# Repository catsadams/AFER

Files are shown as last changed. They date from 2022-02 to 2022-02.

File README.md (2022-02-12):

# AFER
Design and development of  Autonomous Feline Entertainment Robot(AFER) - Project Files
Advanced Control Systems - University of West Florida - Spring 2021

Conference paper abstract
Abstract—The aim of this paper is to present the design and development of a safe and reliable autonomous cat toy for the purposes of entertaining pet cats when human interaction is not feasible. The proposed Autonomous Feline Entertainment Robot (AFER), an autonomous cat toy, is comprised of a table-mounted base, and a robotic arm with two linkages. The AFER Version 1(v1) has a cat-toy affixed to the end of a linkage as the end effector, while the AFER Version 2 (v2) has a passive joint with a string to which a cat toy end effector is attached.  The AFER v1 has 2 Degrees of Freedom (DOF), while the AFER v2 has 3DOF, and both are actuated by servomotors interfaced with an Arduino microcontroller. In order to enable maximum functionality, the AFER is designed with multiple movement patterns or modes for play, as well as the ability to change the specific end effector of the toy. Position control was used for the motion and trajectory planning when developing the movement patterns. The interaction between AFER and two kittens has been evaluated in an experimental scenario, and the results show satisfactory and safe interactions. The AFER can be used as a model for studying effective animal-robot interactions and pet entertainment.

Conference Paper Directory Includes: PDF of final paper, LaTex text files and images pulled for conference paper
Matlab-Arduino Directory Includes: Matlab, Simulink, Arduino code 
CAD Renderings Directory Incudes: SIMULINK renderings of the robot

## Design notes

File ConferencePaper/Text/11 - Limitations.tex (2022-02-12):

There were considerable limitations to this work including lack of access to a robotics lab due to COVID-19 restrictions; as a result, this robot was developed, built, and tested, entirely with at-home robotics equipment. This severely limited the choice of materials and opportunity to attempt multiple builds. 
Additionally, several necessary base assumptions made limited the scope and real-world applicability portions of the work, particularly for the v2. The assumptions for J3 were significant, yet necessary given the circumstances. As a result, the mathematical model for AFER v2 was not able to account for random motion or vibrations of the string, and, therefore, it was not possible to account for those disturbances while planning movement patterns. Additionally, the lack of an encoder on the passive joint, J3, meant that interpreting the success of the movement patterns in any way other than visual, was not possible.
Finally, the preference analysis conducted was based on only two cats and the testing was not repeated multiple times to ensure consistency. A much larger sample size with repetitive testing events would be needed for robust, statistically significant analysis on animal preferences between movement patterns and end effectors \cite{laschi2006design}.

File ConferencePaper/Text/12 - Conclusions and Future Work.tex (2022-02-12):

\subsection {Conclusions}
We developed a simple entertainment robot (two versions) to entertain animals (cats) when they are not attended by humans. Despite limited access to materials, the concepts of the robots were shown to be viable, and the kittens/cats were safely engaged and enjoyed playing with the toy actuated by the robot for as long as the robot was operational. The study is new in the robotics field and possesses significant potential to be used enormously to enhance the entertainment, companionship, and well-being of companionship animals.

\subsection {Future Work}
As expected, prototype models of systems had many issues and often required multiple redesigns and repairs; the AFER systems were no different. Unfortunately, redesigns and more robust construction were beyond the scope of the research in its current iteration. The following issues were identified with the design and would need to be addressed in any future work.
     \par The connection at J1 was small and unstable, and a structural redesign of the robot with a more robust joint or additional support material is necessary for any further work. A redesigned system in conjunction with improved modeling procedures would enable refinement of the control algorithm, and lead to better performance. Additionally, implementing more complex movement patterns would increase applicability.
Due to the nature of the end effector attachment on v1, the computer and electrical components of the system needed to be placed on the ground. For a system that is expected to entertain pets, this is not acceptable. In future iterations, implementing control with a localized chip and batteries would be ideal. If this is achieved, the AFER base could be mounted on a mobile robot unit for further autonomous functionality.
    \par The interactions between cats and the robots will need to be videotaped, which will allow further analysis of the behaviors of the cats with the robots. Machine learning methods such as the reinforcement learning, inverse reinforcement learning or deep reinforcement learning will be used to learn the behaviors of the cats with the robots, which may suggest significant improvements in the design and controls of the robots.

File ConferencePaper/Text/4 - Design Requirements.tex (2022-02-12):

Given the intended use of the AFER platform, the design could not be overly complex and could not require components that would be difficult to acquire for the average person. The robot required the ability to move a cat toy end effector in several, distinct movement patterns for maximum engagement with the animals. 
The robot design also needed adequate safety precautions integrated into the design to prevent injury during operations. The joints and linkages needed adequate softness to prevent injury in the event that the robot made contact with an animal during the course of operations, and any components relating to the control such as wires would be designed such that the animals will not be able to access them.

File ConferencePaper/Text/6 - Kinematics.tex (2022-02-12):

For both versions of the robot, the transformation matrix values were determined using Denavit–Hartenberg (DH) parameters. When solving the kinematics for both v1 and v2, the length of the common normal was identified by the variable r to avoid confusion between variables a and $\alpha$. 

\subsection{Robot Configuration Overviews}
AFER v1 was a 2-DOF robot, actuated by servomotors and an Arduino controller, and modeled such that the cat toy end effector formed a rigid linkage with \textit{l2}. The robot utilized a revolute base joint (J1) and a revolute lift joint (J2) to move the end effector as commanded; the chosen joint configuration allowed the robot to operate along the edges of a hemispherical work envelope with a surface area of $39.9ft^2$, situated about the robot’s center, shown in Fig.5.

\begin{figure}[h!]
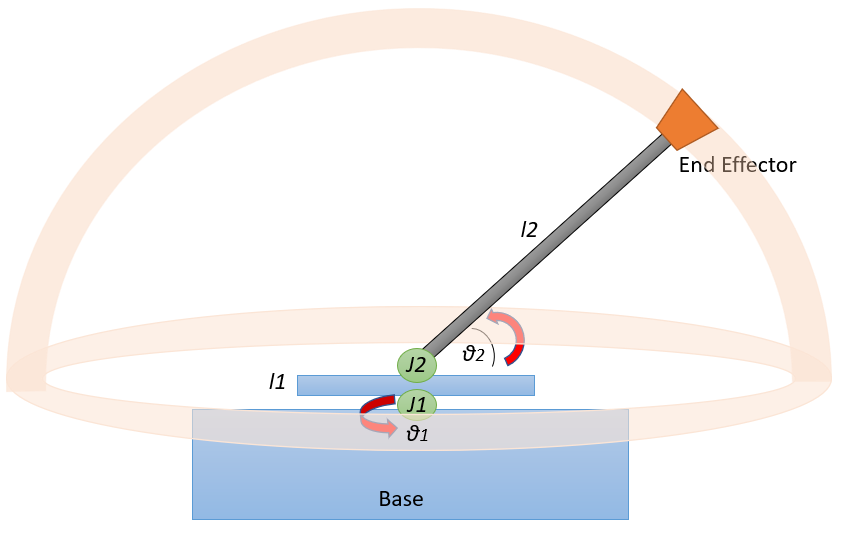
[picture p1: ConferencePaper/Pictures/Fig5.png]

\caption{AFER v1 Work Envelope.}
\label{fig5}
\end{figure}

For this version of the robot, the end effector was mounted directly to \textit{l2}. As the arrangement caused no considerable difficulty when solving the kinematic equations, the mathematical modeling used for v1 closely resembled the real-world robotic build, and the assumptions when solving the kinematic equations were minimal. 
For AFER v2 as shown in Fig.6, the cat toy end effector attached to the rest of the robot via J3, a frictionless joint that was passive in the pitch direction and had no damping. The chosen joint configuration allowed the robot to operate along the edges of a hemispherical workspace with a surface area of $39.9 ft^2$, situated about the robot’s center. The workspace size of v1 and v2 were identical, however the v2 workspace was lower due to the introduction of \textit{l3}. 

\begin{figure}[h!]
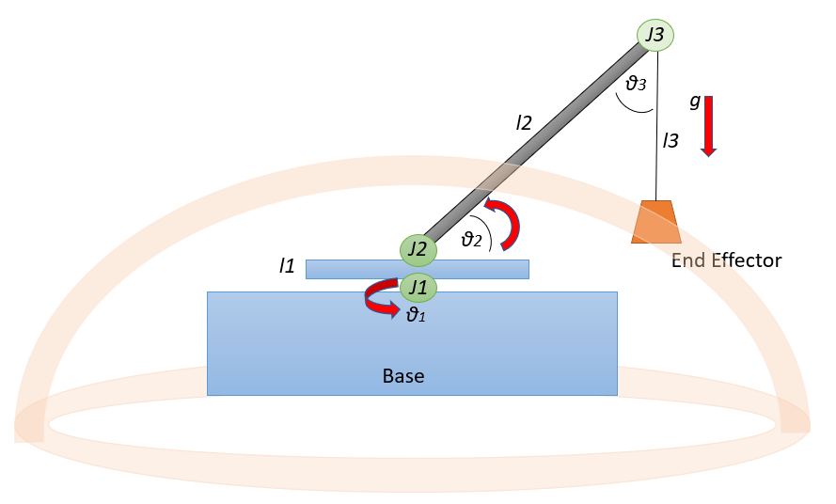
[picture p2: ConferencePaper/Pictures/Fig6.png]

\caption{AFER v2 Work Envelope.}
\label{fig6}
\end{figure}

Realistically, the string attached to the J3 joint on AFER v2 was able to move freely and had factors such as elasticity and conflicting multi-modal vibrations. However, it caused the kinematic equations to be non-linear and extremely difficult, if not impossible, to solve. Therefore, in order to ensure that the kinematics for this version of the robot were useful and solvable, J3 was modeled as a passive joint on a rigid link instead of a compliant linkage. Additionally, the momentum was discounted and the gravity(g) was assumed to be the only force acting upon the suspended end effector. 

\subsection{AFER v1 Forward Kinematics}
The forward kinematics for v1 as a 2-joint robot were relatively simple, but to ensure the solvability of the kinematic model, static stability was assumed for all points. Using the coordinate frames as shown in Fig.5, creating a transformation matrix from the base of the robot to the end effector using a link coordinate diagram was straightforward. The transformation values of r, $\alpha$, d, and $\theta$ are given in Table ~\ref{table:1}.

\begin{center}
\begin{table}[h!]
\centering
\caption{DH PARAMETERS FOR AFER v1}
   \begin{tabular}{ | c | c | c | c | c | }
   \hline
    Point & $d_{i}$ & $\theta_{DHi}$ & $r_{i}$ & $\alpha_{i}$ \\ \hline
    J1 & 0 & 0 & 0 & 0  \\ \hline
    J2 & \textit{l1} & $\theta_{1}$ & 0 & 0 \\ \hline
    EE & \textit{l2} & 0 & 0 & $\theta_{2}$\\ \hline
    \end{tabular}
		\label{table:1}
\end{table}
\end{center}

AFER v1 had a horizontal stroke equal to the length of \textit{l2} and a vertical stroke of \textit{l1} + \textit{l2}. Additionally, the absence of linear actuators indicated that the di values were static. The transformation from the coordinate frame at J1 to the coordinate frame at the end effector was determined as shown in \eqref{1}:

\[
\centering
\begin{bmatrix}
cos\theta_{1} & -sin\theta_{1}cos\theta_{2} & sin\theta_{1}sin\theta_{2} & 0\\
sin\theta_{1} & cos\theta_{1}cos\theta_{2} & -cos\theta_{1}sin\theta_{2} & 0 \\
0 & sin\theta_{2} & cos\theta_{2} & \textit{l2} + \textit{l1} \\
0 & 0 & 0 & 1 \\
\end{bmatrix}
\begin{equation}
\label{eq1}
\end{equation}
\]

\subsection{AFER v2 Forward Kinematics}
The forward kinematics for AFER v2, a 3-joint robot, were relatively simple. When solving the kinematics, static stability was assumed. The DH parameters for J1, J2, and J3 in v2 were identical to the DH parameters for J1, J2 and the end effector (E) of v1 due to the common core configuration of the robot. The values for v2 DH parameters are listed below in Table ~\ref{table:2}. 

\begin{center}
\begin{table}[h]
\centering
\caption{DH PARAMETERS FOR AFER v2}
    \begin{tabular}{ | c | c | c | c |c | }
    \hline
    Point & \ $d_{i}$ & $\theta_{DHi}$ & $r_{i}$ & $\alpha_{i}$ \\ \hline
    J1 & 0 & 0 & 0 & 0  \\ \hline
    J2 & \textit{l1} & $\theta_{1}$ & 0 & 0 \\ \hline
    J3 & \textit{l2} & 0 & 0 & $\theta_{2}$\\ \hline
		E & -\textit{l3} & 0 & 0 & $\theta_{2}+ \frac{\pi}{2}$ \\ \hline
    \end{tabular}
		\label{table:2}
\end{table}
\end{center}

As in v1, v2 had a horizontal stroke equal to the length of \textit{l2}; however, the vertical stroke of \textit{v2} was equal $\textit{l1} + \textit{l2} – \textit{l3}$. Given that there were no linear actuators, the $\textit{d}_{i}$ values were static. The transformation from the coordinate frame at J1 to the coordinate frame at the end effector(E) for v2 was determined as shown in \eqref{2}, where $(\alpha_{E} = \theta_{2} + \frac{\pi}{2})$.

\[
{\tiny
\centering
\label{eq2}
\begin{bmatrix}
c\theta_{1} & -s\theta_{1}c\theta_{2}c\alpha_{E} + s\theta_{1}s\theta_{2}s\alpha_{E} & s\theta_{1}c\theta_{2}s\alpha_{E} + s\theta_{1}s\theta_{2}c\alpha_{E}& -\textit{l3}s\theta_{1}s\theta{2}\\
s\theta_{1} & c\theta_{1}c\theta_{2}c\alpha_{E} - c\theta_{1}s\theta_{2}s\alpha_{E}  & c\theta_{1}c\theta_{2}s\alpha_{E} - c\theta_{1}s\theta_{2}c\alpha_{E}  & 0 \\
0 & s\theta_{2}c\alpha_{E}+ c\theta_{2}s\alpha_{E} & -s\theta_{2}c\alpha_{E}+ c\theta_{2}s\alpha_{E} & -c\theta_{2}\textit{l3} + \textit{l2} +\textit{l1} \\
0 & 0 & 0 & 1 \\
\end{bmatrix}
}
\begin{equation}
\label{eq1}
\end{equation}
\]

\subsection {AFER v1 Inverse Kinematics}
Based upon the hemispherical geometry and low degrees of freedom present in v1, it was simple to solve for the joint angles based on the position of the end effector. Basic trigonometric functions were leveraged to solve for $\theta_{2}$. Since the high torque servomotor creating $\theta_{2}$ had a maximum range of $180^{\circ}$, there was only one solution as in (3).

\begin{equation}
\theta_{2} = sin^{-1}\frac{E_{z} - \textit{l1}}{\textit{l2}} \label{eq3}
\end{equation}

It was easiest to solve for the rotational joint at $\theta_{1}$ by projecting J1 into the $x_{1}, y_{1}$ plane. This allowed the rotational displacement of the joint to be calculated using the simple trigonometric relationships. Due to ambiguity when solving with inverse cosine, inverse tangent was selected for solving for $\theta_{1}$. Since the servomotor at J1 could rotate a full $360^{\circ}$, there were two possible solutions for this joint angle, as (4) and (5) show.

\begin{equation}
\theta_{1} = tan^{-1} 2(E_{x},E_{y})\label{eq4}
\end{equation}

\begin{equation}
\theta_{1} = \pi + tan^{-1} 2(E_{x},E_{y})\label{eq5}
\end{equation}

\subsection{AFER v2 Inverse Kinematics}
For $\theta_{1}$ and $\theta_{2}$, the v2 inverse kinematics was identical to the v1. Solving for $\theta_{3}$ was trivial using the mathematical properties of triangles. Given that the sum of the interior angles of a triangle are always equal to $180^{\circ}$, and the assumption of static stability for J3, (6) was used to define $\theta_{3}$:

\begin{equation}
\theta_{3} = \frac{pi}{2} - \theta_{2} \label{eq6}
\end{equation}

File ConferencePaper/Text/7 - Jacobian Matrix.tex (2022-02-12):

The Jacobian matrices for AFER v1 and v2 were solved in order to provide insight on the relationships between the joint space and Cartesian space when planning the movement patterns. The Jacobian was determined by using standard spherical-Cartesian transformation equations as in (7), and the substitution values for v1 were $\theta = \theta_{1}$, $\phi = \theta_{2}$, and $r = \textit{l2}$.

\[
\centering
\begin{bmatrix}
sin\theta_{2}cos\theta_{1} & \textit{l2}cos\theta_{2}cos\theta_{1} & -\textit{l2}sin\theta_{2}sin\theta_{1} \\
sin\theta_{2}sin\theta_{1} & \textit{l2}cos\theta_{2}sin\theta_{1} & \textit{l2}sin\theta_{2}cos\theta_{1}  \\
cos\theta_{2} & -sin\theta_{2} & 0 \\
\end{bmatrix}
\begin{equation}
\label{eq7}
\end{equation}
\]

The Jacobians for AFER v1 and v2 were identical due to the common core configuration between AFER v1 and v2 and the assumptions regarding J3 in v2. The Jacobian matrix for joints 1 and 2 remained unchanged, and supposing static equilibrium, velocity at the end effector along the y axis will always be zero. The end effector velocity along the x axis could change and, given that the value of $\theta_{3}$ was dependent upon $\theta_{2}$, would always change at the same rate as the velocity at J3. As a result, the Jacobian in (7) sufficed for AFER v2 as well.

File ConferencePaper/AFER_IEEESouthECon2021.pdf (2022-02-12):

# Design and Development of an Autonomous Feline Entertainment Robot (AFER) for Studying Animal-Robot Interactions

Catherine S. Adams
Dept. of Electrical and Computer Engineering University of West Florida Pensacola, FL, U.S.A.
csa21@students.uwf.edu
S. M. Mizanoor Rahman
Dept. of Intelligent Systems and Robotics University of West Florida Pensacola, FL, U.S.A.
smrahman@uwf.edu

Abstract—The aim of this paper is to present the design and development of a safe and reliable autonomous cat toy for the purposes of entertaining pet cats when human interaction is not feasible. The proposed Autonomous Feline Entertainment Robot (AFER), an autonomous cat toy, is comprised of a tablemounted base, and a robotic arm with two linkages. The AFER Version 1(v1) has a cat-toy affixed to the end of a linkage as the end effector, while the AFER Version 2 (v2) has a passive joint with a string to which a cat toy end effector is attached. The AFER v1 has 2 Degrees of Freedom (DOF), while the AFER v2 has 3DOF, and both are actuated by servomotors interfaced with an Arduino microcontroller. In order to enable maximum functionality, the AFER is designed with multiple movement patterns or modes for play, as well as the ability to change the specific end effector of the toy. Position control was used for the motion and trajectory planning when developing the movement patterns. The interaction between AFER and two kittens has been evaluated in an experimental scenario, and the results show satisfactory and safe interactions. The AFER can be used as a model for studying effective animal-robot interactions and pet entertainment.

Index Terms——Animal-robot interaction, pet entertainment robot, autonomous cat toy, robot design, design evaluation

I. INTRODUCTION

In 2020, pet adoptions steadily rose and the market for autonomous pet entertainment robots is increased concurrently. Pets require mental stimulation and physical exercise to avoid boredom, anxiety, and poor behaviors associated with under stimulation.

A. Background – Animal Welfare Standards

‘The Five Freedoms’ were first developed by the Brambell Committee Report in 1965 as the minimum standard for ethical treatment of farm animals. These freedoms are summarized as: freedom from thirst, hunger, and malnutrition; freedom from

Approved for Public Release, Distribution Unlimited. Public Release Case Number 20-3462. The author’s affiliation with The MITRE Corporation is provided for identification purposes only, and is not intended to convey or imply MITRE’s concurrence with, or support for, the positions, opinions, or viewpoints expressed by the author.’©2020 The MITRE Corporation. ALL RIGHTS RESERVED.

discomfort; freedom from pain, injury, and disease; freedom to express normal behavior; freedom from fear and distress [1]. From the Five Freedoms, researchers created a framework for assessing the welfare of zoo and lab animals as well. In the case of companion animals, the responsibility for meeting these needs and providing a healthy and engaging environment as well as the environmental enrichment falls upon their owners. The term ‘environmental enrichment’ can be used to describe “changes, modifications and other interventions made to the environment with the aim of improving the welfare of the animals living in that environment [2].”

B. Problem Identification – Providing Adequate Mental Stimulation for Indoor-only Cats
The American Veterinary Medical Association, Humane Society of the United States, most American animal shelters, and American veterinarians recommend that domestic cats be kept indoors in both urban and suburban living situations. This recommendation considers several factors; outdoor domestic cats can pose a threat to the balance of local ecosystems, and, generally, indoor domestic cats are much healthier and have longer lifespans compared to their outdoor counterparts [2]. Remaining indoors protects the cats from outdoor hazards such as vehicles and predators, however, it also provides a much lower degree of stimulation and sensory engagement than the outdoors. This lack of engagement can lead to boredom, stress, and ultimately destructive behaviors of the cats [3]. Therefore, indoor cats require enrichment activities, yet awareness of enrichment needs is often lacking among pet owners. Some pet owners may find it particularly difficult to meet the sensory and occupational needs of younger cats and kittens, as they tend to have more energy and require more active play time. In order to provide a more enriching environment for these cats, a robot designed to engage and play with the cats could be activated when their owner is otherwise occupied. The robot should provide effective stimulation and engagement, and be safe for the cats. However, there are extremely few reports in the literature investigating effective examples of such entertainment robots for cats or pets.

C. Objectives

This project aimed to develop a robot that could fulfill this purpose. Thus, the objective of this paper is to present the design, development, construction, and evaluation of an autonomous toy-like animal robot - the Autonomous Feline Entertainment Robot (AFER) with its two Versions 1(v1) and 2(v2). The robot developed, built, and tested was intended to entertain two six-month old kittens when they were unable to be attended by a human. The AFER system aims to assist pet owners with meeting their needs towards entertaining their pets.

II. RELATED WORKS

A literature review was conducted in several areas to ensure robust design and experimentation practices. Previous robotics studies involving pet-robot interactions were investigated to ascertain the level of previous research conducted for similar or analogous robots. Behavioral studies on cats regarding toy and play preferences were researched to inform robot movement patterns and selection of the cat toy to be used as the end effector.

A. Studies on Pet-Robot Interaction

Two relevant papers on pet entertainment robots and the related pet-robot interaction were available. The first paper was a design innovation exploring a possible design for an autonomous pet care robot intended for dogs [4]. The study provided interesting ideas regarding movement and food rewards, but the robot has not yet been prototyped or tested. The second study focused on various types of robots and their effectiveness when entertaining a cat [5]. This was more directly applicable to our objectives than the first study, offered good insight into robot design considerations specific to cats, and defined the concept of Animal-Robot Interaction (ARI). The model in [4] is the preliminary design for a “home service robot for pet caring.” This robot design focused on playing, feeding, and otherwise caring for a dog – a set of functions which are not currently available in any single commercial pet-care robots. The research in [5] aimed to examine the possibility of a robot replacing a human for the purposes of short-term pet care as well as use the definition and practices of Human-Robot Interaction (HRI) to create a working understanding and set of criteria for Animal-Robot Interaction (ARI). The identified differences between HRI characteristics and ARI characteristics largely hinge on the ability of the user to communicate clearly with the robot. Since a human user has the ability to command the robot to complete a certain task, and an animal user does not, a Pet Care Robot (PCR) must have the ability to accept commands from human users and also have adequate sensing and processing ability to interpret pet-provided signals and respond appropriately to the defined pet behavior. Currently, there are no commercially available robots designed for pet interaction that can monitor and adjust functions based upon the emotional state of the pet.

B. Cat Behavioral Studies

Many studies on cat play behaviors have been conducted and in reviewing several of those, movement was consistently found to be one of the crucial components when attempting to elicit play behaviors in cats. Movement was found to be particularly effective when the toy was moved away from the cat or in a manner that mimicked prey [2], [6]. However, examples of effective, real-time and safe interactions between robot toys and cats were limited.

III. DESIGN REQUIREMENTS

Given the intended use of the AFER platform, the design could not be overly complex and could not require components that would be difficult to acquire for the average person. The robot required the ability to move a cat toy end effector in several, distinct movement patterns for maximum engagement with the animals. The robot design also needed adequate safety precautions integrated into the design to prevent injury during operations. The joints and linkages needed adequate softness to prevent injury in the event that the robot made contact with an animal during the course of operations, and any components relating to the control such as wires would be designed such that the animals will not be able to access them.

IV. MATERIALS AND METHODS

A. Materials List

The following materials were used to design, assemble, and test the AFER systems: Arduino controller (1), USB Cable (1), CAT 6e Cable (1), a computer with the capability to run Arduino Integrated Development Environment (IDE), Autodesk Fusion 360 Computer Aided Design(CAD) software and Open Source Fritzing Hardware Prototyping Software, a servomotor with 360◦
rotation (1), High-torque servomotor with 180◦
rotation (1), Servomotor horn – 4 prong (1), servo horn 2-prong (1), 30 row bread board (1), composite dowel
(1) , 3-D printed Polylactic Acid (PLA) l1, 3-D printed PLA dowel mount (1), 3-D printed PLA servomotor mounts (2), plywood base (1), wood clamps (2), Cat Toys – Feather (1) / Mouse (1), C-Clamp (2), Bosch 12v Lithium Ion Battery Power Drill (1), IRWIN 15 Piece Drill bit set – sizes 1
16 to
3/8(1), String (1), Bolts (10), Superglue (1), Sewing ruler (1), Tape measure (1), 3-D printer – Monoprice Maker Select v2, PLA filament, etc.
B. Methods

The following high-level steps were used:

- Step 1: Design and build the system
- Step 2: Solve the kinematics and Jacobian
- Step 3: Develop and implement movement patterns
- Step 4: Experimental evaluation of the design
- Step 5: Performance Analysis

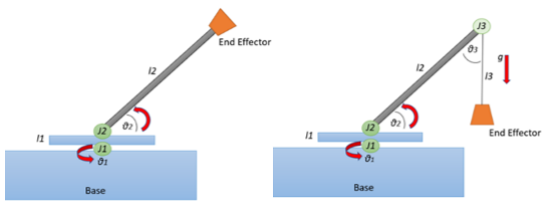
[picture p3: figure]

Fig. 1. AFER v1 and v2 sketches.

1) Designing the Robot: The first step in designing the robot was to hand sketch the initial block diagram design for AFER v1 and v2. The hand sketches were then converted to basic diagrams on a computer, shown in Fig.1 below:
For both AFER versions: J1 is the first joint, J2 the second joint, l1 the height of the rotating platform between J1 and J2, l2 the length of the actuated arm, θ1 the angle of rotation about the z-axis, and θ2 the angle of l2 with respect to the xaxis. AFER v2 has three additional parameters: J3 as joint 3, l3 as the length of the string attached to J3, and θ3 as the angle between l2 and l3. Once the overall design was determined, the pieces requiring CAD rendering - l1, servomotor mount 1 (SM1), servomotor mount 2 (SM2), and the dowel mount (DM) – were sketched by hand. Once sketched, measurements of the servomotors and dowel were taken using a sewing ruler and tape measure. Those measurements were then used to inform the exact size and shape of the part builds. The Autodesk Fusion 360 software was used to build and render each of the parts. Fig.2 shows the CAD rendering and completed print of the SM1 piece, as an example.

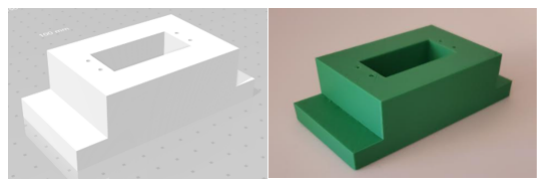
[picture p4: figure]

Fig. 2. AFER SM 1 CAD rendering (left) and printed piece (right).

2) Building the Robot: When designing the pieces to be 3-D printed, there were sets of bolt holes that were not rendered in CAD to allow greater flexibility while assembling and to allow for adjustments to ensure proper alignment of the axes. The necessary holes for those bolts were measured and drilled individually during the assembly process. The robot was built beginning with the topmost piece and working down to the base to simplify the process of establishing the z-axis for joints 1 and 2 as coincident. On the front plate, a hole was drilled at a height that would ensure the center axis of the dowel would intersect orthogonally with the rotational axis of J2, and the servomotor horns were screwed into DM. Servo Mount 2 (SM2) was then mounted to the side of l1, positioning J2 directly above J1 to avoid altering the z axis. A wiring port and inset bolt holes were also drilled into SM2. A similar process was used on l1. The high torque servomotor was then fitted into SM2 and attached using the printed bolt holes; once secured to the mount, the servo was connected to DM. Subsequently, the 360◦
rotation servomotor was fitted and bolted into the mount. Mounting the 4-prong servomotor horn to l1 was accomplished using super glue and screws. The SM2, DM, l1 configuration was placed onto the servomotor in SM1 once the glue had dried. The final build step was to attach the AFER robot to the plywood base. The same 3-D printed core parts were used for both v1 and v2; to switch between versions, the directly connected end effector was replaced with a string and the end effectors were then attached to the string. Fig.3 shows the fully assembled AFER v1 and v2.

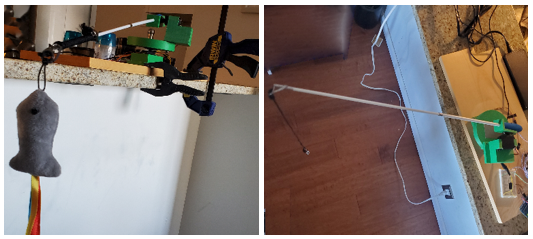
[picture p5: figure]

Fig. 3. Fully assembled AFER v1 (left) and v2 (right).

Wiring for the Arduino and two servomotors was accomplished by stripping the CAT 6e cable and using the interior wires to connect between Arduino ports, the bread board, and the positive, negative and control wires for both servomotors. To ensure adequate power for running multiple servomotors, the bread board was connected to an external 5v power source. Fig.4 is a wiring diagram built using an open source wiring tool called Fritzing to illustrate the connections needed to power and control the AFER core configuration and subsequently, AFER v1 and v2.
3) Solving the Kinematics and Jacobian: The process for solving the kinematics is described in greater depth in Section
V. The process for deriving the Jacobian for AFER v1 and v2 is described in Section VI.
4) Developing and Implementing Movement Patterns: The movement patterns selected were a simple back-and-forth oscillation, an up-and-down oscillation, and a combination of both types of oscillation. Position control was used for all three movement patterns. The Arduino Servo Library contains a function “Sweep” which swings the shaft of the servomotor back and forth across a 180◦
arc. The source code for this function was used as a starting point for both the up-and-down and back-and-forth oscillation patterns [7]. Each oscillation pattern was comprised of two loops, one to sweep the servo from 0 to the maximum angle - 45◦

for servo 2 and 180◦
for servo 1 – and a second loop to sweep the servo from the maximum angle back to 0. The combination of both oscillation patterns was achieved by combining the four loops from the previous code into two loops that actuated both

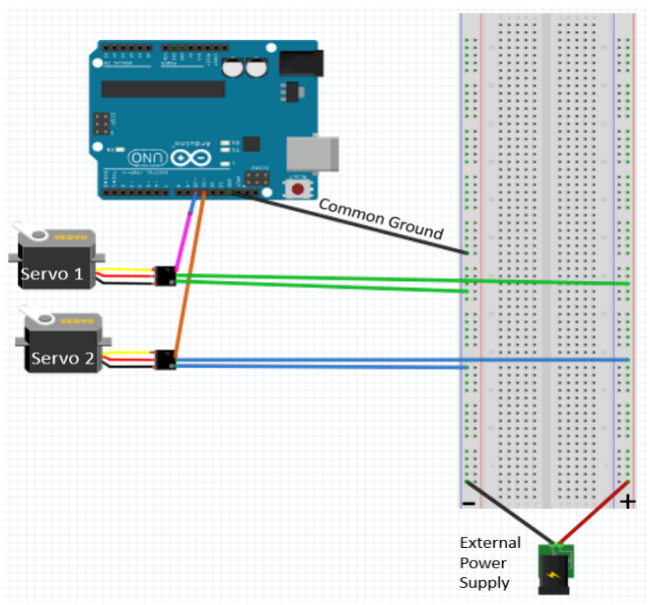
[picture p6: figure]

Fig. 4. AFER Circuit Diagram.

servos simultaneously. All three of those motion patterns were simplistic and did not require any complex path planning or trajectory generation to implement. To avoid erratic robot behavior during initial testing, the robot pieces were separated, and the code was tested on the servomotors with no load. The initial testing involved sweeping servo 1 in a 90◦ arc
and servo 2 in a 45◦
arc; the testing with those parameters was successful. The code was then tested on the full common core unit. Upon initial assembly and motion testing, the servo horn and motor at J1 continuously became disconnected after 2-3 oscillations. To add stability, the horn and motor were superglued together. Once the glue dried, J1 was significantly more stable and able to withstand the necessary continuous oscillation. Once AFER was securely assembled, it became clear that 180◦ was too large of an angle for servo 1 when accounting for the full length of l1 and space in which the kittens could play; the sweep angle for servo 1 was, therefore, reduced to 90◦
. Additionally, to resolve an increment error, the servo 1 code was updated to increment by 2 rather than 1.
5) Test Subjects: The robot was tested on two kittens – one male, one female – each approximately six months old. The female kitten, named Klunk, was solid black; she weighed 6.1lbs at the time of testing. Her demeanor was timid and easily startled. The male kitten, named Traximus, was black with white tuxedo markings; he weighed 6.4lbs at the time of testing, and his demeanor was outgoing and curious.
6) Experimentation and Testing (Evaluation) : Once fully assembled, the robot was tested to ensure that it could be operated effectively and safely prior to the introduction of the test subjects. The experimentation and test procedures are documented in greater depth in Section VII.
7) Safety Considerations: The robot was designed with the following safety considerations:
- The Servomotors selected do not create adequate force to cause damage to the kittens.
- The dowel selected was made of partially compliant material that was unlikely to cause injury if it collided with the one of the kittens.
- Trajectories that simulated a wrapping movement were avoided to minimize the likelihood of accidentally tangling the kittens in the AFER v2 string.
- For AFER v1, the robot was placed on a box and secured with C clamps to prevent it from falling.
- For AFER v2, a set of C clamps were used to secure the robot base to a table and ensure the kittens could not pull the robot onto themselves during play and cause injury.
- The wires used to connect the robot and laptop were covered with cardboard or paper as much as possible to prevent the kittens from chewing the wires as well as protect from accidental shocks.
8) Performance Analysis: Performance of the robot was ascertained predominately by visually observing the behavior of the system and the test subject’s reactions to it. Some servo data was observed in the Arduino Serial Monitor to verify the system movement patterns were implemented properly. See Section VII for further details.
C. Assumptions
The design and modeling assumptions are below:
- The encoders in the servomotors had sufficient precision for this task
- For v1, all linkages were modeled as rigid linkages
- For v2, J3 was modeled as a passive joint that was frictionless, had no damping, and had no elasticity
- For v2, the link between J3 and the end effector was assumed to be rigid
- For both robots, when solving the kinematics, static stability would be assumed at all points
V. KINEMATICS
For both versions of the robot, the transformation matrix values were determined using Denavit–Hartenberg (DH) parameters. When solving the kinematics for both v1 and v2, the length of the common normal was identified by the variable r to avoid confusion between variables a and α.
A. Robot Configuration Overviews
AFER v1 was a 2-DOF robot, actuated by servomotors and an Arduino controller, and modeled such that the cat toy end effector formed a rigid linkage with l2. The robot utilized a revolute base joint (J1) and a revolute lift joint (J2) to move the end effector as commanded; the chosen joint configuration allowed the robot to operate along the edges of a hemispherical work envelope with a surface area of 39.9f t²
, situated about
the robot’s center, shown in Fig.5.
For this version of the robot, the end effector was mounted directly to l2. As the arrangement caused no considerable difficulty when solving the kinematic equations, the mathematical modeling used for v1 closely resembled the real-world


Fig. 5. AFER v1 Work Envelope.

robotic build, and the assumptions when solving the kinematic equations were minimal. For AFER v2 as shown in Fig.6, the cat toy end effector attached to the rest of the robot via J3, a frictionless joint that was passive in the pitch direction and had no damping. The chosen joint configuration allowed the robot to operate along the edges of a hemispherical workspace with a surface area of 39.9f t²
, situated about the robot’s center. The workspace size of v1 and v2 were identical, however the v2 workspace was lower due to the introduction of l3.


Fig. 6. AFER v2 Work Envelope.

Realistically, the string attached to the J3 joint on AFER v2 was able to move freely and had factors such as elasticity and conflicting multi-modal vibrations. However, it caused the kinematic equations to be non-linear and extremely difficult, if not impossible, to solve. Therefore, in order to ensure that the kinematics for this version of the robot were useful and solvable, J3 was modeled as a passive joint on a rigid link instead of a compliant linkage. Additionally, the momentum was discounted and the gravity(g) was assumed to be the only force acting upon the suspended end effector.

B. AFER v1 Forward Kinematics
The forward kinematics for v1 as a 2-joint robot were relatively simple, but to ensure the solvability of the kinematic model, static stability was assumed for all points. Using the coordinate frames as shown in Fig.5, creating a transformation matrix from the base of the robot to the end effector using a link coordinate diagram was straightforward. The transformation values of r, α, d, and θ are given in Table I.

TABLE I
DH PARAMETERS FOR AFER V1
Point | di | θDHi | ri | αi
J1 | 0 | 0 | 0 | 0
J2 | l1 | θ1 | 0 | 0
EE | l2 | 0 | 0 | θ2

AFER v1 had a horizontal stroke equal to the length of l2 and a vertical stroke of l1 + l2. Additionally, the absence of linear actuators indicated that the di values were static. The transformation from the coordinate frame at J1 to the coordinate frame at the end effector was determined as shown in (1):
cosθ1 | −sinθ1cosθ2 | sinθ1sinθ2 | 0
sinθ1 | cosθ1cosθ2 | −cosθ1sinθ2 | 0
0 | sinθ2 | cosθ2 | l2 + l1
0 | 0 | 0 | 1

(1)

C. AFER v2 Forward Kinematics
The forward kinematics for AFER v2, a 3-joint robot, were relatively simple. When solving the kinematics, static stability was assumed. The DH parameters for J1, J2, and J3 in v2 were identical to the DH parameters for J1, J2 and the end effector (E) of v1 due to the common core configuration of the robot. The values for v2 DH parameters are listed below in Table II.

TABLE II
DH PARAMETERS FOR AFER V2
Point | di | θDHi | ri | αi
J1 | 0 | 0 | 0 | 0
J2 | l1 | θ1 | 0 | 0
J3 | l2 | 0 | 0 | θ2
E | -l3 | 0 | 0 | θ2 + π
2

As in v1, v2 had a horizontal stroke equal to the length of l2; however, the vertical stroke of v2 was equal l1 + l2–l3. Given that there were no linear actuators, the di values were static. The transformation from the coordinate frame at J1 to the coordinate frame at the end effector(E) for v2 was determined as shown in (2), where (αE = θ2 +

π
2

).

cθ1 | −sθ1cθ2cαE + sθ1sθ2sαE | sθ1cθ2sαE + sθ1sθ2cαE | −l3sθ1sθ2
sθ1 | cθ1cθ2cαE − cθ1sθ2sαE | cθ1cθ2sαE − cθ1sθ2cαE | 0
0 | sθ2cαE + cθ2sαE | −sθ2cαE + cθ2sαE | −cθ2l3 + l2 + l1
0 | 0 | 0 | 1 |

(2)

D. AFER v1 Inverse Kinematics

Based upon the hemispherical geometry and low degrees of freedom present in v1, it was simple to solve for the joint angles based on the position of the end effector. Basic trigonometric functions were leveraged to solve for θ2. Since the high torque servomotor creating θ2 had a maximum range of 180◦
, there was only one solution as in (3).

θ2 = sin⁻¹ Ez − l1
l2

(3)

It was easiest to solve for the rotational joint at θ1 by projecting J1 into the x1, y1 plane. This allowed the rotational displacement of the joint to be calculated using the simple trigonometric relationships. Due to ambiguity when solving with inverse cosine, inverse tangent was selected for solving for θ1. Since the servomotor at J1 could rotate a full 360◦ ,
there were two possible solutions for this joint angle, as (4) and (5) show.

θ1 = tan⁻¹
2(Ex, Ey) | (4)

θ1 = π + tan⁻¹
2(Ex, Ey) | (5)
E. AFER v2 Inverse Kinematics

For θ1 and θ2, the v2 inverse kinematics was identical to the v1. Solving for θ3 was trivial using the mathematical properties of triangles. Given that the sum of the interior angles of a triangle are always equal to 180◦
, and the assumption of
static stability for J3, (6) was used to define θ3:

θ3 =

pi
2
− θ2 | (6)

VI. JACOBIAN MATRIX

The Jacobian matrices for AFER v1 and v2 were solved in order to provide insight on the relationships between the joint space and Cartesian space when planning the movement patterns. The Jacobian was determined by using standard spherical-Cartesian transformation equations as in (7), and the substitution values for v1 were θ = θ1, φ = θ2, and r = l2.
sinθ2cosθ1 | l2cosθ2cosθ1 | −l2sinθ2sinθ1
sinθ2sinθ1 | l2cosθ2sinθ1 | l2sinθ2cosθ1
cosθ2 | −sinθ2 | 0
- (7)

The Jacobians for AFER v1 and v2 were identical due to the common core configuration between AFER v1 and v2 and the assumptions regarding J3 in v2. The Jacobian matrix for joints 1 and 2 remained unchanged, and supposing static equilibrium, velocity at the end effector along the y axis will always be zero. The end effector velocity along the x axis could change and, given that the value of θ3 was dependent upon θ2, would always change at the same rate as the velocity at J3. As a result, the Jacobian in (7) sufficed for AFER v2 as well.

VII. EXPERIMENTAL EVALUATION OF PERFORMANCE
Testing the fully assembled robot was conducted in two analogous but distinct phases, one for each configuration of AFER. Phase 1 tested the performance of AFER v1, and Phase 2 involved the same testing for AFER v2. The testing questions answered for both versions are listed below:
- Is the base adequately secured?
- Does the up/down oscillation function under load?
- Does the left/right oscillation function under load?
- Does the combined oscillation function under load?
- Do the chosen trajectories avoid self-collision?
- Are the wires adequately concealed?
- Have all obstacles been removed from the area?
- Is the end effector securely attached?
Results for all tests were collected using visual observation, and servo outputs. Visual observation was the primary method of ascertaining proper behavior of the system, however the servo output data was also analyzed in real time to verify proper operation of the robot. Once the robot was determined to be operational and safe, the test subjects were introduced. The following procedure was used to ascertain the test subject’s interaction preferences between AFER v1 and AFER v2 robots and the type of end effector. Those steps were recorded and evaluated based on visual observation:
- Introduce test subjects (cats) to base configuration
- Assemble AFER v1
- Introduce test subjects to v1 configuration
- Allow test subjects to interact with operational AFER v1 with End Effector 1 attached
- Allow test subjects to interact with operational AFER v1 with End Effector 2 attached
- Observe and record test subject behavior
- Repeat steps 2-6 with the AFER v2 configuration
Fig. 7 shows the engagement of kittens with AFER v1 and v2. Basic standards for ethical treatment of animals were obeyed when observing the cats/kittens engaged with the robots [1].

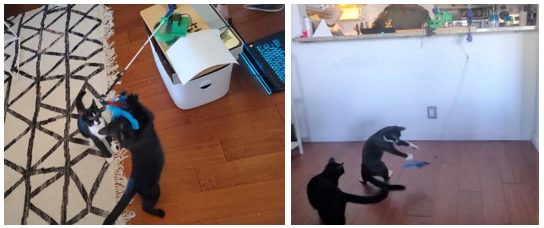
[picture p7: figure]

Fig. 7. Kittens engaged with AFER v1 (left) and v2 (right).

VIII. RESULTS AND PERFORMANCE ANALYSIS
Initial testing of movement patterns on the completely assembled robot was extremely successful, and the robot followed the linear movement pattern as expected. Introducing both kittens to the base configuration and AFER v1 configuration was simple and uneventful. Neither animal exhibited any of the common fear or stress reactions – ears flattened, sitting low, hiding or hissing – and both engaged with the end effector toy once the robot was in motion. For the analysis of the pet-robot interaction shown in the tables below, Active Engagement (AE) was defined as the kitten chasing and catching or attempting to catch the end effector; Passive Engagement (PE) was defined as the kitten watching and showing interest in the robot or end effector, but not attempting to chase or catch. No Engagement (NE) was used to describe time in which the kitten was completely disinterested in the device. Engagement behaviors were observed over a 5-minute experimentation period. Comparisons of engagement for AFER v1 is shown in Table 3.

TABLE III
AFER V1 INTERACTION
Kitten | AE | %AE | PE | %PE | NE | %NE
Male | 45s | 15% | 3min25s | 68% | 50s | 17%
Female | 3min45s | 75% | 45s | 15% | 0s | 0%

The kittens were also not frightened by the AFER v2 configuration, however, the female kitten seemed more wary and the male kitten dominated the play window. Of the 5 minutes allotted for testing, only 2 minutes were completed prior to the failure of the J1 joint. Time of engagement is shown in Table 4.

TABLE IV
AFER V2 INTERACTION
Kitten | AE | %AE | PE | %PE | NE | %NE
Male | 2min | 100% | 0s | 0% | 0s | 0%
Female | 0s | 0% | 2min | 100% | 0s | 0%

The J1 failure occurred when the top portion of the robot including J2 and l1 separated from the base and J1 at the servomotor-servo horn connection. Despite the superglue used at that connection, the force created by the kittens playing with the end effector was too much for the robot to withstand. Testing of the robot was halted at this point and repairs were attempted. Although testing was cut short, both versions of the robot proved viable concepts, and highly interesting to the kittens. Both kittens engaged with both versions of the robot, though each seemed to have a distinct preference in version.

IX. POTENTIAL IMPACTS
The primary goal and impact of this research was to increase the environmental enrichment of a home thereby increasing the health and happiness of two kittens residing there. These kittens now have greater access to a safe and engaging nonstatic toy. This impact has a broad applicability and, with further work, has the capacity to impact and positively influence on the well-being of other cats as well. The market for robotic toys for entertaining pets is growing rapidly and a robot such as AFER meets many of the necessary requirements for a robotic pet toy and has the potential for monetization. Monetizing or selling the robot design to a commercial entity for mass production would allow other pet owners to provide a higher level of engagement to their pets as well. This would be particularly useful during crisis situations similar to COVID-19, as the pandemic caused an unprecedented increase in individuals fostering or adopting pets from animal shelters [8]. Therefore, a large number of first-time pet owners and individuals with multiple pets could highly benefit from having robotic toys like the one presented herein to assist with the enrichment and mental stimulation of their pets.
X. LIMITATIONS
There were considerable limitations to this work including lack of access to a robotics lab due to COVID-19 restrictions; as a result, this robot was developed, built, and tested, entirely with at-home robotics equipment. This severely limited the choice of materials and opportunity to attempt multiple builds. Additionally, several necessary base assumptions made limited the scope and real-world applicability portions of the work, particularly for the v2. The assumptions for J3 were significant, yet necessary given the circumstances. As a result, the mathematical model for AFER v2 was not able to account for random motion or vibrations of the string, and, therefore, it was not possible to account for those disturbances while planning movement patterns. Additionally, the lack of an encoder on the passive joint, J3, meant that interpreting the success of the movement patterns in any way other than visual, was not possible. Finally, the preference analysis conducted was based on only two cats and the testing was not repeated multiple times to ensure consistency. A much larger sample size with repetitive testing events would be needed for robust, statistically significant analysis on animal preferences between movement patterns and end effectors [9].

XI. CONCLUSIONS AND FUTURE WORK

A. Conclusions
We developed a simple entertainment robot (two versions) to entertain animals (cats) when they are not attended by humans. Despite limited access to materials, the concepts of the robots were shown to be viable, and the kittens/cats were safely engaged and enjoyed playing with the toy actuated by the robot for as long as the robot was operational. The study is new in the robotics field and possesses significant potential to be used enormously to enhance the entertainment, companionship, and well-being of companionship animals.
B. Future Work
As expected, prototype models of systems had many issues and often required multiple redesigns and repairs; the AFER systems were no different. Unfortunately, redesigns and more robust construction were beyond the scope of the research in its current iteration. The following issues were identified with the design and would need to be addressed in any future work.

The connection at J1 was small and unstable, and a structural redesign of the robot with a more robust joint or additional support material is necessary for any further work. A redesigned system in conjunction with improved modeling procedures would enable refinement of the control algorithm, and lead to better performance. Additionally, implementing more complex movement patterns would increase applicability. Due to the nature of the end effector attachment on v1, the computer and electrical components of the system needed to be placed on the ground. For a system that is expected to entertain pets, this is not acceptable. In future iterations, implementing control with a localized chip and batteries would be ideal. If this is achieved, the AFER base could be mounted on a mobile robot unit for further autonomous functionality.
The interactions between cats and the robots will need to be videotaped, which will allow further analysis of the behaviors of the cats with the robots. Machine learning methods such as the reinforcement learning, inverse reinforcement learning or deep reinforcement learning will be used to learn the behaviors of the cats with the robots, which may suggest significant improvements in the design and controls of the robots.

ACKNOWLEDGMENTS
Thanks to Matthew Bender, Ph.D. for the use of his 3-D printer, and special thanks to Cameron Ridgewell for allowing me to use his extra servomotors and Arduino microcontroller as well as his editing, comments, and general robotics guidance.

REFERENCES

[1] F. Brambell, “Report of the technical committee to enquire into the welfare of animals kept under intensive livestock husbandry systems.”
[2] I. Rochlitz, “A review of the housing requirements of domestic cats (felis silvestris catus) kept in the home,” Applied Animal Behaviour Science, vol. 93, no. 1-2, pp. 97–109, 2005.
[3] D. L. Wells, “Sensory stimulation as environmental enrichment for captive animals: a review,” Applied Animal Behaviour Science, vol. 118, no. 1-2, pp. 1–11, 2009.
[4] W. Deng, Y. Shi, C. Li, T. Zou, and C. Tian, “Design of home service robot for pet caring,” in Journal of Physics: Conference Series, vol. 1550, no. 2. IOP Publishing, 2020, p. 022026.
[5] J.-H. Kim, S.-H. Choi, D. Kim, J. Kim, and M. Cho, “Animal-robot interaction for pet caring,” in 2009 IEEE International Symposium on Computational Intelligence in Robotics and Automation-(CIRA). IEEE, 2009, pp. 159–164.
[6] P. Leyhausen, B. A. Tonkin et al., Cat behaviour. The predatory and social behaviour of domestic and wild cats. Garland STPM Press., 1979.
[7] S. | Fitzgerald, | Sweep, | ver. | 11/08/13, | Arduino | Tu-
torial | Library, | 2020. | [Online]. | [Online]. | Available:
https://www.arduino.cc/en/Tutorial/LibraryExamples/Sweep
[8] N. Delgadillo, “So many people are trying to adopt or foster pets that local shelters are having trouble meeting demand,” Apr 2020.
[Online]. | Available: | https://dcist.com/story/20/04/21/so-many-people-
are-trying-to-adopt-or-foster-pets-that-local-shelters-are-having-troublemeeting-demand/
[9] C. Laschi, B. Mazzolai, F. Patane, V. Mattoli, P. Dario, H. Ishii, M. Ogura, `
S. Kurisu, A. Komura, and A. Takanishi, “Design and development of a legged rat robot for studying animal-robot interaction,” in The First IEEE/RAS-EMBS International Conference on Biomedical Robotics and Biomechatronics, 2006. BioRob 2006. IEEE, 2006, pp. 631–636.

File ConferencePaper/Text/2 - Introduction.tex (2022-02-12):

In 2020, pet adoptions steadily rose and the market for autonomous pet entertainment robots is increased concurrently. Pets require mental stimulation and physical exercise to avoid boredom, anxiety, and poor behaviors associated with under stimulation. 

\subsection {Background – Animal Welfare Standards}
‘The Five Freedoms’ were first developed by the Brambell Committee Report in 1965 as the minimum standard for ethical treatment of farm animals. These freedoms are summarized as:
freedom from thirst, hunger, and malnutrition; freedom from discomfort; freedom from pain, injury, and disease; freedom to express normal behavior; freedom from fear and distress \cite{Brambell1965ReportOT}.
   From the Five Freedoms, researchers created a framework for assessing the welfare of zoo and lab animals as well. In the case of companion animals, the responsibility for meeting these needs and providing a healthy and engaging environment as well as the environmental enrichment falls upon their owners. The term ‘environmental enrichment’ can be used to describe “changes, modifications and other interventions made to the environment with the aim of improving the welfare of the animals living in that environment \cite{rochlitz2005review}.”

\subsection {Problem Identification – Providing Adequate Mental Stimulation for Indoor-only Cats}
The American Veterinary Medical Association, Humane Society of the United States, most American animal shelters, and American veterinarians recommend that domestic cats be kept indoors in both urban and suburban living situations. This recommendation considers several factors; outdoor domestic cats can pose a threat to the balance of local ecosystems, and, generally, indoor domestic cats are much healthier and have longer lifespans compared to their outdoor counterparts \cite{rochlitz2005review}. Remaining indoors protects the cats from outdoor hazards such as vehicles and predators, however, it also provides a much lower degree of stimulation and sensory engagement than the outdoors. This lack of engagement can lead to boredom, stress, and ultimately destructive behaviors of the cats \cite{wells2009sensory}. Therefore, indoor cats require enrichment activities, yet awareness of enrichment needs is often lacking among pet owners.
  Some pet owners may find it particularly difficult to meet the sensory and occupational needs of younger cats and kittens, as they tend to have more energy and require more active play time. In order to provide a more enriching environment for these cats, a robot designed to engage and play with the cats could be activated when their owner is otherwise occupied. The robot should provide effective stimulation and engagement, and be safe for the cats. However, there are extremely few reports in the literature investigating effective examples of such entertainment robots for cats or pets. 

\subsection{Objectives}
This project aimed to develop a robot that could fulfill this purpose. Thus, the objective of this paper is to present the design, development, construction, and evaluation of an autonomous toy-like animal robot - the Autonomous Feline Entertainment Robot (AFER) with its two Versions 1(v1) and 2(v2). The robot developed, built, and tested was intended to entertain two six-month old kittens when they were unable to be attended by a human. The AFER system aims to assist pet owners with meeting their needs towards entertaining their pets.

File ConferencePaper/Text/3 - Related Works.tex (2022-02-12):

A literature review was conducted in several areas to ensure robust design and experimentation practices.  Previous robotics studies involving pet-robot interactions were investigated to ascertain the level of previous research conducted for similar or analogous robots. Behavioral studies on cats regarding toy and play preferences were researched to inform robot movement patterns and selection of the cat toy to be used as the end effector. 

\subsection{Studies on Pet-Robot Interaction}
Two relevant papers on pet entertainment robots and the related pet-robot interaction were available. The first paper was a design innovation exploring a possible design for an autonomous pet care robot intended for dogs \cite{deng2020design}. The study provided interesting ideas regarding movement and food rewards, but the robot has not yet been prototyped or tested. The second study focused on various types of robots and their effectiveness when entertaining a cat \cite{kim2009animal}. This was more directly applicable to our objectives than the first study, offered good insight into robot design considerations specific to cats, and defined the concept of Animal-Robot Interaction (ARI). 
The model in \cite{deng2020design} is the preliminary design for a “home service robot for pet caring.” This robot design focused on playing, feeding, and otherwise caring for a dog – a set of functions which are not currently available in any single commercial pet-care robots. The research in \cite{kim2009animal} aimed to examine the possibility of a robot replacing a human for the purposes of short-term pet care as well as use the definition and practices of Human-Robot Interaction (HRI) to create a working understanding and set of criteria for Animal-Robot Interaction (ARI). The identified differences between HRI characteristics and ARI characteristics largely hinge on the ability of the user to communicate clearly with the robot. Since a human user has the ability to command the robot to complete a certain task, and an animal user does not, a Pet Care Robot (PCR) must have the ability to accept commands from human users and also have adequate sensing and processing ability to interpret pet-provided signals and respond appropriately to the defined pet behavior. Currently, there are no commercially available robots designed for pet interaction that can monitor and adjust functions based upon the emotional state of the pet.

\subsection{Cat Behavioral Studies}
Many studies on cat play behaviors have been conducted and in reviewing several of those, movement was consistently found to be one of the crucial components when attempting to elicit play behaviors in cats. Movement was found to be particularly effective when the toy was moved away from the cat or in a manner that mimicked prey \cite{rochlitz2005review}, \cite{leyhausen1979cat}. However, examples of effective, real-time and safe interactions between robot toys and cats were limited.

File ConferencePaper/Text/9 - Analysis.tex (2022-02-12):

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

\begin{center}
\begin{table}[htbp]
\centering
\caption{AFER v1 INTERACTION}
    \begin{tabular}{ |c|c|c|c|c|c|c| }
    \hline
    Kitten & AE & \%AE & PE & \%PE & NE & \%NE \\ \hline
    Male & 45s & 15\% & 3min25s & 68\% & 50s & 17\%  \\ \hline
    Female & 3min45s & 75\% & 45s & 15\% & 0s & 0\% \\ \hline
    \end{tabular}
		\label{table:3}
\end{table}
\end{center}

The kittens were also not frightened by the AFER v2 configuration, however, the female kitten seemed more wary and the male kitten dominated the play window. Of the 5 minutes allotted for testing, only 2 minutes were completed prior to the failure of the J1 joint. Time of engagement is shown in Table 4.

\begin{center}
\begin{table}[h]
\centering
\caption{AFER v2 INTERACTION}
    \begin{tabular}{ |c|c|c|c|c|c|c| }
    \hline
    Kitten & AE & \%AE & PE & \%PE & NE & \%NE \\ \hline
    Male & 2min & 100\% & 0s & 0\% & 0s & 0\%  \\ \hline
    Female & 0s & 0\% & 2min & 100\% & 0s & 0\% \\ \hline
    \end{tabular}
		\label{table:4}
\end{table}
\end{center}

The J1 failure occurred when the top portion of the robot including J2 and \textit{l1} separated from the base and J1 at the servomotor-servo horn connection. Despite the superglue used at that connection, the force created by the kittens playing with the end effector was too much for the robot to withstand. Testing of the robot was halted at this point and repairs were attempted. 
Although testing was cut short, both versions of the robot proved viable concepts, and highly interesting to the kittens. Both kittens engaged with both versions of the robot, though each seemed to have a distinct preference in version.

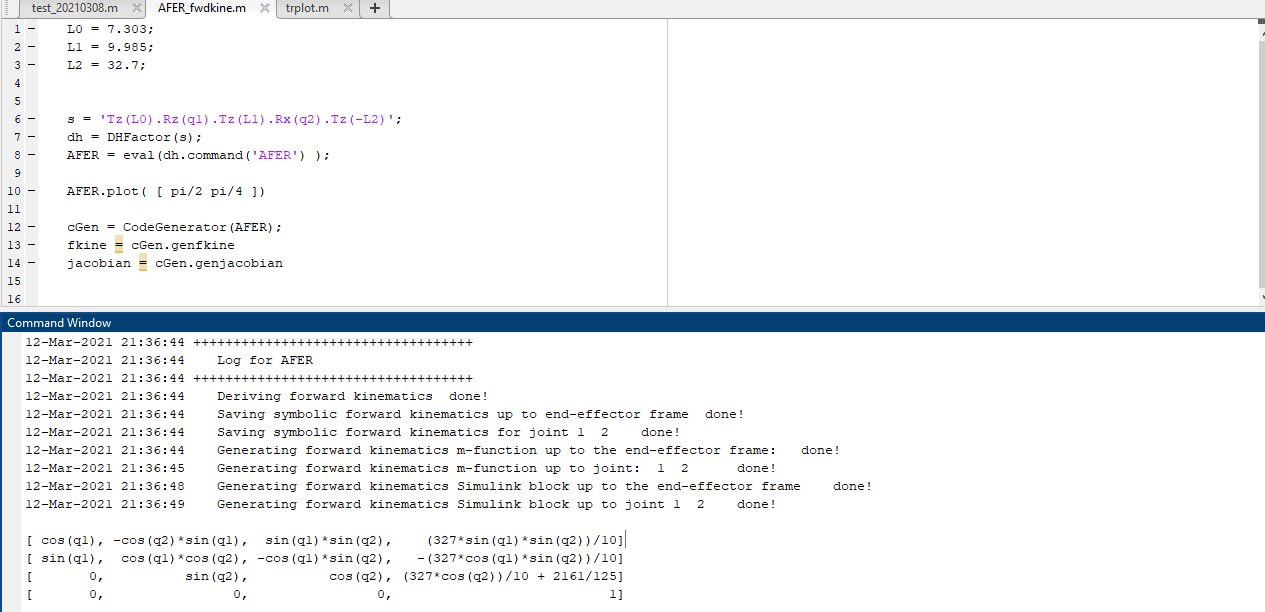
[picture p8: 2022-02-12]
Matlab-Arduino/AFER_FWD Kinematics.PNG

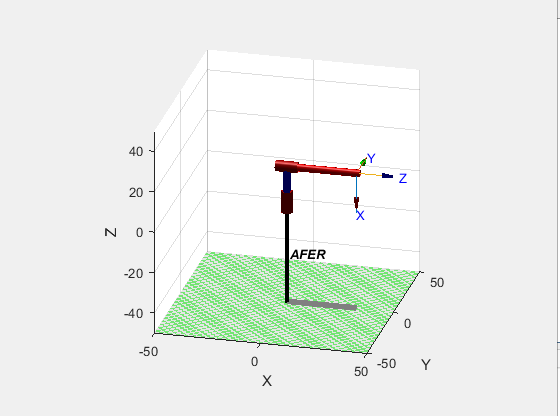
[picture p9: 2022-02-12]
Matlab-Arduino/AFER_StickDiagram.PNG

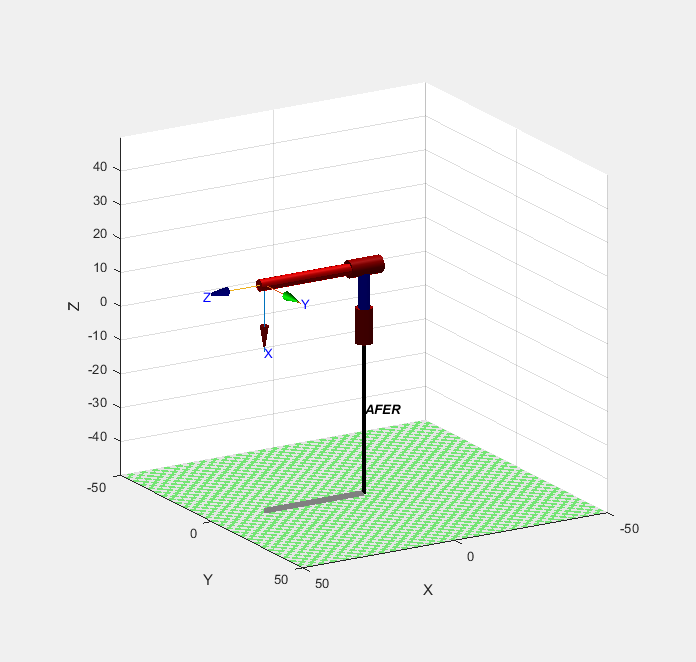
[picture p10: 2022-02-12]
Matlab-Arduino/Afer_stick2.PNG

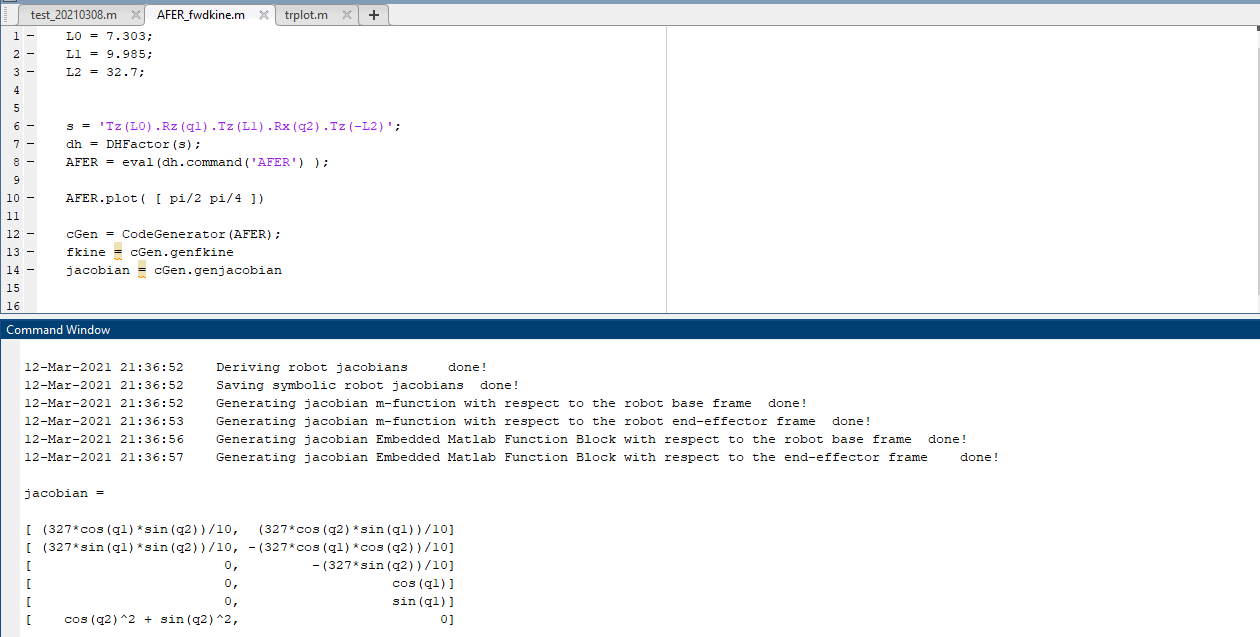
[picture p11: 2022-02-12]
Matlab-Arduino/AFER_Jacobian.PNG

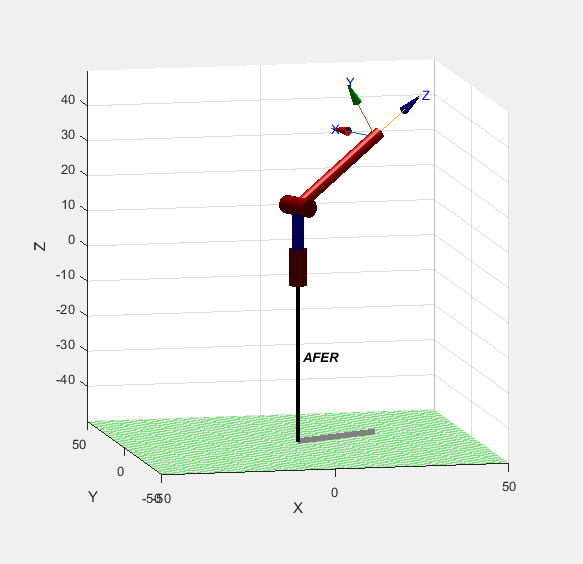
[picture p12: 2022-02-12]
Matlab-Arduino/AFER_stick3.PNG

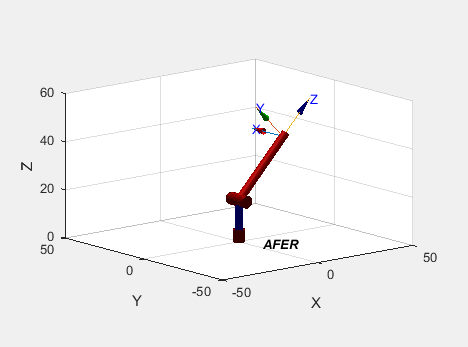
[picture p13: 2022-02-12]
Matlab-Arduino/AFER_stick4.PNG

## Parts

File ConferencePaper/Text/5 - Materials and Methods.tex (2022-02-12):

\subsection{Materials List}
The following materials were used to design, assemble, and test the AFER systems: Arduino controller (1), USB Cable (1), CAT 6e Cable (1), a computer with the capability to run Arduino Integrated Development Environment (IDE), Autodesk Fusion 360 Computer Aided Design(CAD) software and Open Source Fritzing Hardware Prototyping Software, a servomotor with $360^{\circ}$ rotation (1), High-torque servomotor with $180^{\circ}$ rotation (1), Servomotor horn – 4 prong (1), servo horn 2-prong (1), 30 row bread board (1), composite dowel (1) , 3-D printed Polylactic Acid (PLA) \textit{l1}, 3-D printed PLA dowel mount (1), 3-D printed PLA servomotor mounts (2), plywood base (1), wood clamps (2), Cat Toys – Feather (1) / Mouse (1), C-Clamp (2), Bosch 12v Lithium Ion Battery Power Drill (1), IRWIN 15 Piece Drill bit set – sizes $\frac{1}{16}$ to $\frac{3}{8} (1)$, String (1), Bolts (10), Superglue (1), Sewing ruler (1), Tape measure (1), 3-D printer – Monoprice Maker Select v2, PLA filament, etc. 

\subsection{Methods}
The following high-level steps were used:
\begin{itemize}
\item Step 1: Design and build the system
\item Step 2: Solve the kinematics and Jacobian
\item Step 3: Develop and implement movement patterns
\item Step 4: Experimental evaluation of the design
\item Step 5: Performance Analysis
\end{itemize}

\subsubsection {Designing the Robot}
The first step in designing the robot was to hand sketch the initial block diagram design for AFER v1 and v2. The hand sketches were then converted to basic diagrams on a computer, shown in Fig.1 below:

\begin{figure}[h!]
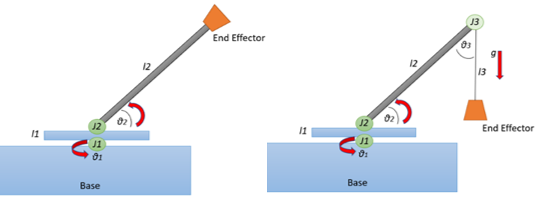
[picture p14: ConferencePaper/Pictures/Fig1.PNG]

\caption{AFER v1 and v2 sketches.}
\label{1}
\end{figure}

For both AFER versions: J1 is the first joint, J2 the second joint,  \textit{l1} the height of the rotating platform between J1 and J2,  \textit{l2} the length of the actuated arm, $\theta_{1}$ the angle of rotation about the z-axis, and $\theta_{2}$ the angle of \textit{l2} with respect to the x-axis. AFER v2 has three additional parameters: J3 as joint 3, \textit{l3} as the length of the string attached to J3, and $\theta_{3}$ as the angle between \textit{l2} and \textit{l3}.
Once the overall design was determined, the pieces requiring CAD rendering - \textit{l1}, servomotor mount 1 (SM1), servomotor mount 2 (SM2), and the dowel mount (DM) – were sketched by hand. Once sketched, measurements of the servomotors and dowel were taken using a sewing ruler and tape measure. Those measurements were then used to inform the exact size and shape of the part builds. The Autodesk Fusion 360 software was used to build and render each of the parts. Fig.2 shows the CAD rendering and completed print of the SM1 piece, as an example.

\begin{figure}[h!]
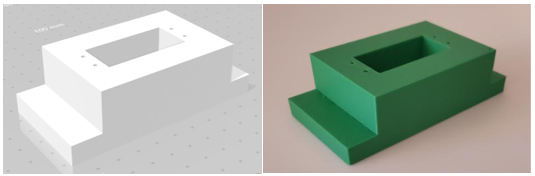
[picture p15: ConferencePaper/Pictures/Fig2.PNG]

\caption{AFER SM 1 CAD rendering (left) and printed piece (right).}
\label{2}
\end{figure}

\subsubsection{Building the Robot}
When designing the pieces to be 3-D printed, there were sets of bolt holes that were not rendered in CAD to allow greater flexibility while assembling and to allow for adjustments to ensure proper alignment of the axes. The necessary holes for those bolts were measured and drilled individually during the assembly process. The robot was built beginning with the topmost piece and working down to the base to simplify the process of establishing the z-axis for joints 1 and 2 as coincident. 
On the front plate, a hole was drilled at a height that would ensure the center axis of the dowel would intersect orthogonally with the rotational axis of J2, and the servomotor horns were screwed into DM. Servo Mount 2 (SM2) was then mounted to the side of \textit{l1}, positioning J2 directly above J1 to avoid altering the z axis. A wiring port and inset bolt holes were also drilled into SM2. A similar process was used on \textit{l1}.
The high torque servomotor was then fitted into SM2 and attached using the printed bolt holes; once secured to the mount, the servo was connected to DM. Subsequently, the $360^{\circ}$rotation servomotor was fitted and bolted into the mount. Mounting the 4-prong servomotor horn to \textit{l1} was accomplished using super glue and screws. The SM2, DM, \textit{l1} configuration was placed onto the servomotor in SM1 once the glue had dried. 
The final build step was to attach the AFER robot to the plywood base. The same 3-D printed core parts were used for both v1 and v2; to switch between versions, the directly connected end effector was replaced with a string and the end effectors were then attached to the string. Fig.3 shows the fully assembled AFER v1 and v2.

\begin{figure}[h!]

\caption{Fully assembled AFER v1 (left) and v2 (right).}
\label{3}
\end{figure}

Wiring for the Arduino and two servomotors was accomplished by stripping the CAT 6e cable and using the interior wires to connect between Arduino ports, the bread board, and the positive, negative and control wires for both servomotors. To ensure adequate power for running multiple servomotors, the bread board was connected to an external 5v power source. Fig.4 is a wiring diagram built using an open source wiring tool called Fritzing to illustrate the connections needed to power and control the AFER core configuration and subsequently, AFER v1 and v2.

\begin{figure}[h!]
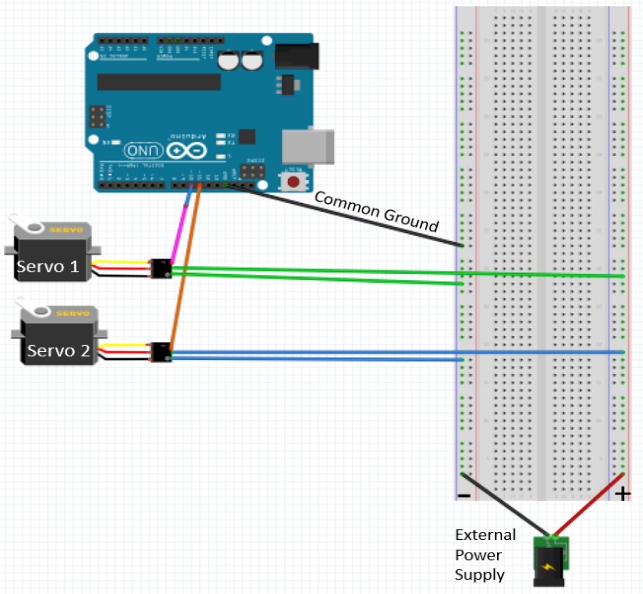
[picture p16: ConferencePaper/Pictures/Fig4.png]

\caption{AFER Circuit Diagram.}
\label{4}
\end{figure}

\subsubsection{Solving the Kinematics and Jacobian}
The process for solving the kinematics is described in greater depth in Section V. The process for deriving the Jacobian for AFER v1 and v2 is described in Section VI.

\subsubsection{Developing and Implementing Movement Patterns}
The movement patterns selected were a simple back-and-forth oscillation, an up-and-down oscillation, and a combination of both types of oscillation. Position control was used for all three movement patterns. 
The Arduino Servo Library contains a function “Sweep” which swings the shaft of the servomotor back and forth across a $180^{\circ}$ arc. The source code for this function was used as a starting point for both the up-and-down and back-and-forth oscillation patterns \cite{Arduino2020sweep}. Each oscillation pattern was comprised of two loops, one to sweep the servo from 0 to the maximum angle - $45^{\circ}$ for servo 2 and $180^{\circ}$ for servo 1 – and a second loop to sweep the servo from the maximum angle back to 0. The combination of both oscillation patterns was achieved by combining the four loops from the previous code into two loops that actuated both servos simultaneously.
All three of those motion patterns were simplistic and did not require any complex path planning or trajectory generation to implement. To avoid erratic robot behavior during initial testing, the robot pieces were separated, and the code was tested on the servomotors with no load. The initial testing involved sweeping servo 1 in a $90^{\circ}$ arc and servo 2 in a $45^{\circ}$ arc; the testing with those parameters was successful.
The code was then tested on the full common core unit. Upon initial assembly and motion testing, the servo horn and motor at J1 continuously became disconnected after 2-3 oscillations. To add stability, the horn and motor were superglued together. Once the glue dried, J1 was significantly more stable and able to withstand the necessary continuous oscillation. 
Once AFER was securely assembled, it became clear that $180^{\circ}$ was too large of an angle for servo 1 when accounting for the full length of \textit{l1} and space in which the kittens could play; the sweep angle for servo 1 was, therefore, reduced to $90^{\circ}$. Additionally, to resolve an increment error, the servo 1 code was updated to increment by 2 rather than 1. 

\subsubsection{Test Subjects}
The robot was tested on two kittens – one male, one female – each approximately six months old. The female kitten, named Klunk, was solid black; she weighed 6.1lbs at the time of testing. Her demeanor was timid and easily startled. The male kitten, named Traximus, was black with white tuxedo markings; he weighed 6.4lbs at the time of testing, and his demeanor was outgoing and curious.

\subsubsection{ Experimentation and Testing (Evaluation) }
Once fully assembled, the robot was tested to ensure that it could be operated effectively and safely prior to the introduction of the test subjects. The experimentation and test procedures are documented in greater depth in Section VII.

\subsubsection{Safety Considerations}
The robot was designed with the following safety considerations: 
\begin{itemize}
\item The Servomotors selected do not create adequate force to cause damage to the kittens.
\item The dowel selected was made of partially compliant material that was unlikely to cause injury if it collided with the one of the kittens.
\item Trajectories that simulated a wrapping movement were avoided to minimize the likelihood of accidentally tangling the kittens in the AFER v2 string.
\item For AFER v1, the robot was placed on a box and secured with C clamps to prevent it from falling.
\item For AFER v2, a set of C clamps were used to secure the robot base to a table and ensure the kittens could not pull the robot onto themselves during play and cause injury.
\item The wires used to connect the robot and laptop were covered with cardboard or paper as much as possible to prevent the kittens from chewing the wires as well as protect from accidental shocks.
\end{itemize}

\subsubsection{Performance Analysis}
Performance of the robot was ascertained predominately by visually observing the behavior of the system and the test subject’s reactions to it. Some servo data was observed in the Arduino Serial Monitor to verify the system movement patterns were implemented properly. See Section VII for further details.

\subsection{Assumptions}
The design and modeling assumptions are below:
\begin{itemize}
\item The encoders in the servomotors had sufficient precision for this task
\item For v1, all linkages were modeled as rigid linkages 
\item For v2, J3 was modeled as a passive joint that was frictionless, had no damping, and had no elasticity
\item For v2, the link between J3 and the end effector was assumed to be rigid
\item For both robots, when solving the kinematics, static stability would be assumed at all points
\end{itemize}

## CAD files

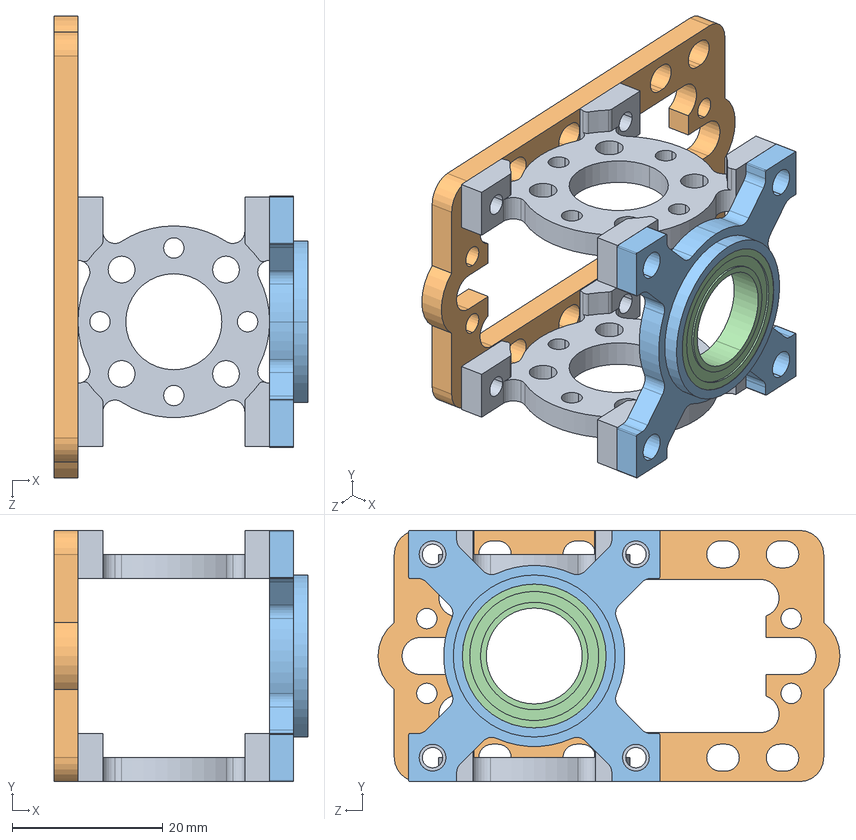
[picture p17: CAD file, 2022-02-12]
CAD Renderings/637110/ServoHub.SLDASM
33.7 x 33.3 x 61.2 mm
545420.step x 2
575112.step
535118.STEP
.5 x .75 non flanged bearing.STEP

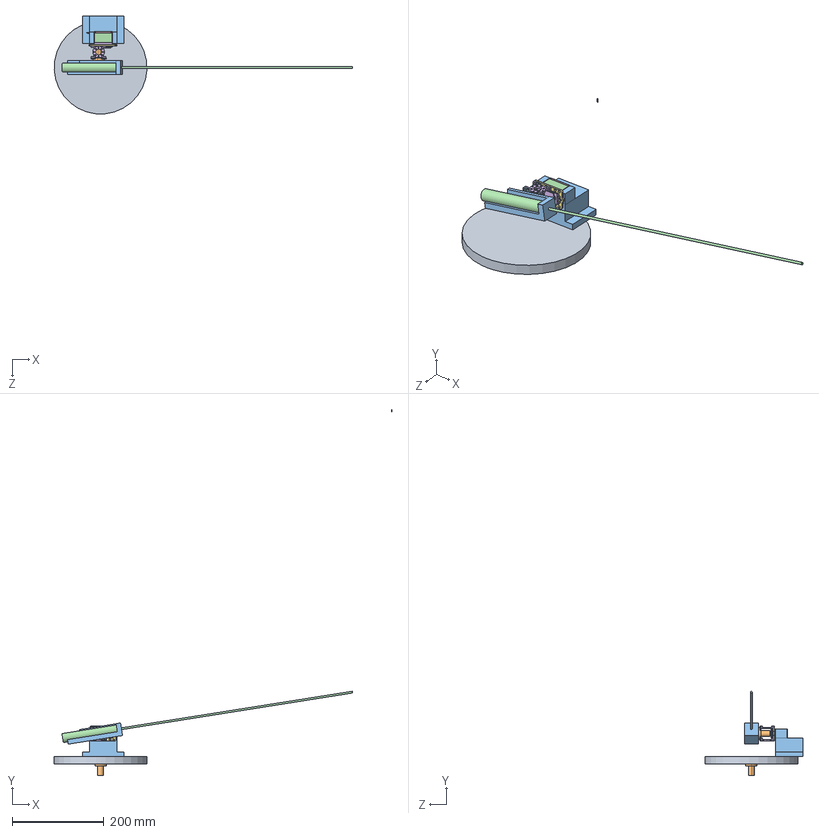
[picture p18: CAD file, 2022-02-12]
CAD Renderings/TopAssembly.SLDASM
735.9 x 798.2 x 743.4 mm
l1_pine
525122.step
Servo Mount2 v1_imported
User Library-Hitec HS-422 servo motor assy_Hitec HS-422 -001
User Library-Hitec HS-422 servo motor assy_Hitec HS-422 -002
User Library-Hitec HS-422 servo motor assy_Hitec HS-422 -003
User Library-Hitec HS-422 servo motor assy_c1 spline-001
User Library-Hitec HS-422 servo motor assy_servo_motor-005
User Library-Hitec HS-422 servo motor assy_copper_core_1 x 3
User Library-Hitec HS-422 servo motor assy_insulator_blk
User Library-Hitec HS-422 servo motor assy_insulator_red
User Library-Hitec HS-422 servo motor assy_insulator_ylw
User Library-Hitec HS-422 servo motor assy_ISO 7049 - C-H ST 2.2 x 4.5 - C - H x 4
545420.step x 2
575112.step
535118.STEP
.5 x .75 non flanged bearing.STEP
DM v1_imported
Dowel

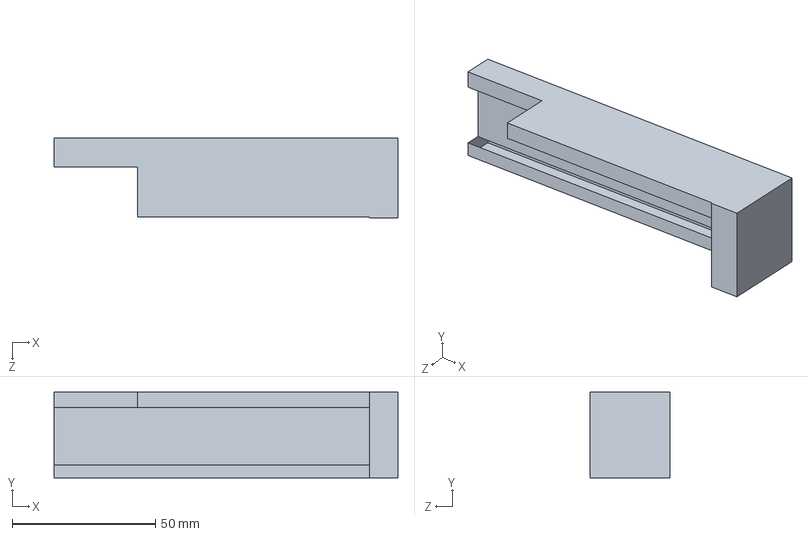
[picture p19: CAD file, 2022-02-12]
CAD Renderings/637110/Assem1.SLDASM
120.0 x 30.0 x 27.8 mm

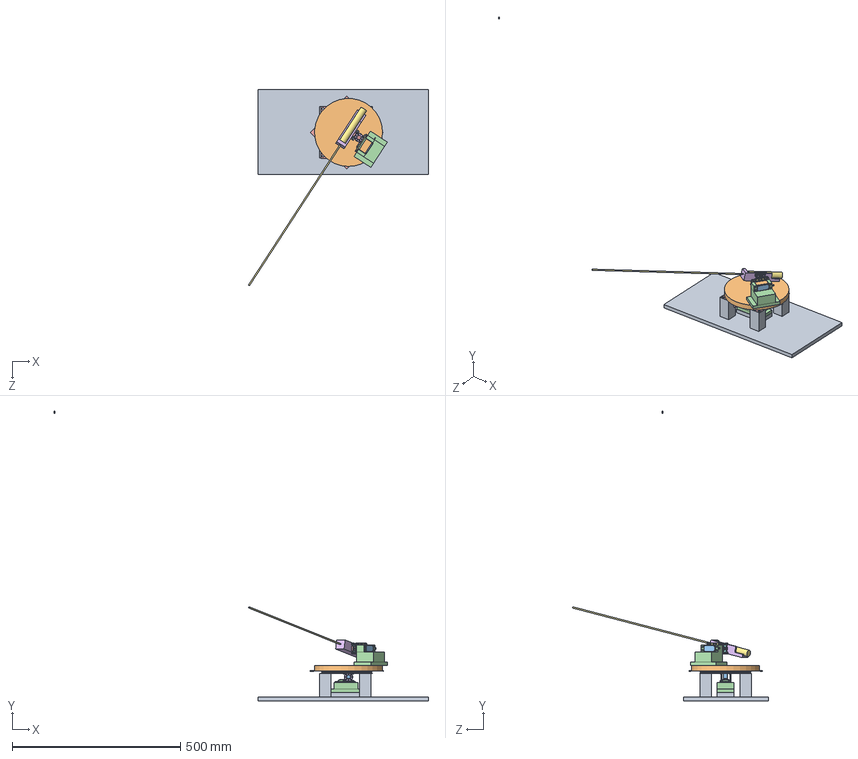
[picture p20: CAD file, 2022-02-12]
CAD Renderings/AFER_Complete.SLDASM
1113.0 x 862.3 x 584.8 mm
Base_legs
User Library-Hitec HS-422 servo motor assy_Hitec HS-422 -001 x 2
User Library-Hitec HS-422 servo motor assy_Hitec HS-422 -002 x 2
User Library-Hitec HS-422 servo motor assy_Hitec HS-422 -003 x 2
User Library-Hitec HS-422 servo motor assy_c1 spline-001 x 2
User Library-Hitec HS-422 servo motor assy_servo_motor-005 x 2
User Library-Hitec HS-422 servo motor assy_copper_core_1 x 6
User Library-Hitec HS-422 servo motor assy_insulator_blk x 2
User Library-Hitec HS-422 servo motor assy_insulator_red x 2
User Library-Hitec HS-422 servo motor assy_insulator_ylw x 2
User Library-Hitec HS-422 servo motor assy_ISO 7049 - C-H ST 2.2 x 4.5 - C - H x 8
Servo Mount1 v4_imported
1544T100_LUBRICATED CORROSION-RESISTANT TURNTABLE
545420.step x 4
575112.step x 2
535118.STEP x 2
.5 x .75 non flanged bearing.STEP x 2
l1_pine
525122.step
Servo Mount2 v1_imported
DM v1_imported
Dowel

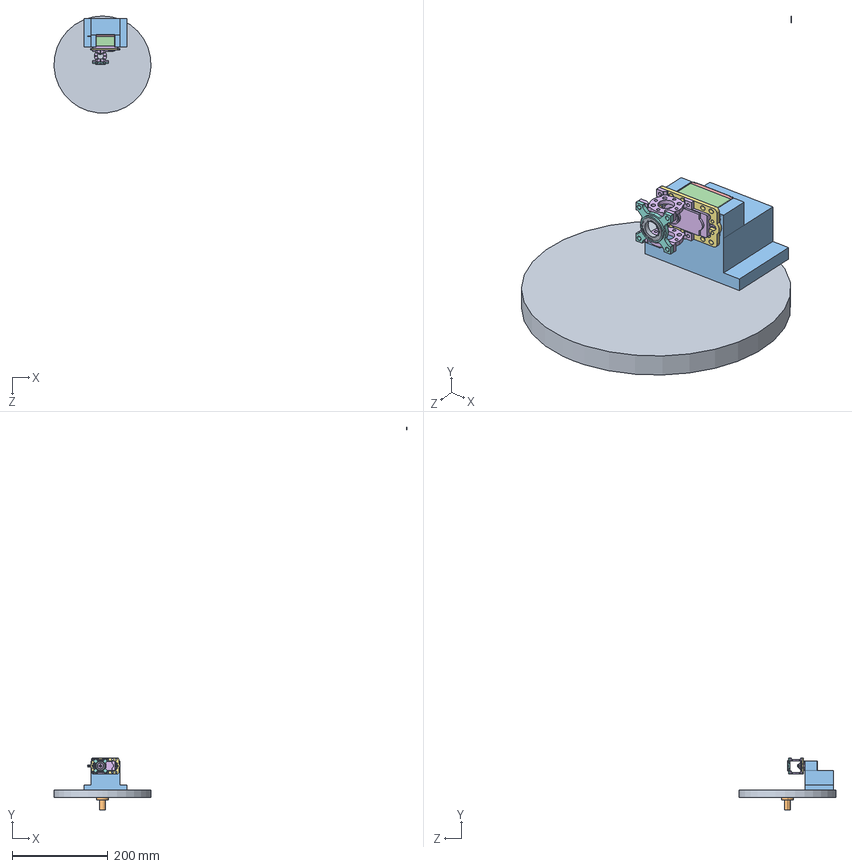
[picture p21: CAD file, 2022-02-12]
CAD Renderings/RotationLevel1.SLDASM
735.9 x 798.2 x 748.5 mm
l1_pine
525122.step
Servo Mount2 v1_imported
User Library-Hitec HS-422 servo motor assy_Hitec HS-422 -001
User Library-Hitec HS-422 servo motor assy_Hitec HS-422 -002
User Library-Hitec HS-422 servo motor assy_Hitec HS-422 -003
User Library-Hitec HS-422 servo motor assy_c1 spline-001
User Library-Hitec HS-422 servo motor assy_servo_motor-005
User Library-Hitec HS-422 servo motor assy_copper_core_1 x 3
User Library-Hitec HS-422 servo motor assy_insulator_blk
User Library-Hitec HS-422 servo motor assy_insulator_red
User Library-Hitec HS-422 servo motor assy_insulator_ylw
User Library-Hitec HS-422 servo motor assy_ISO 7049 - C-H ST 2.2 x 4.5 - C - H x 4
545420.step x 2
575112.step
535118.STEP
.5 x .75 non flanged bearing.STEP

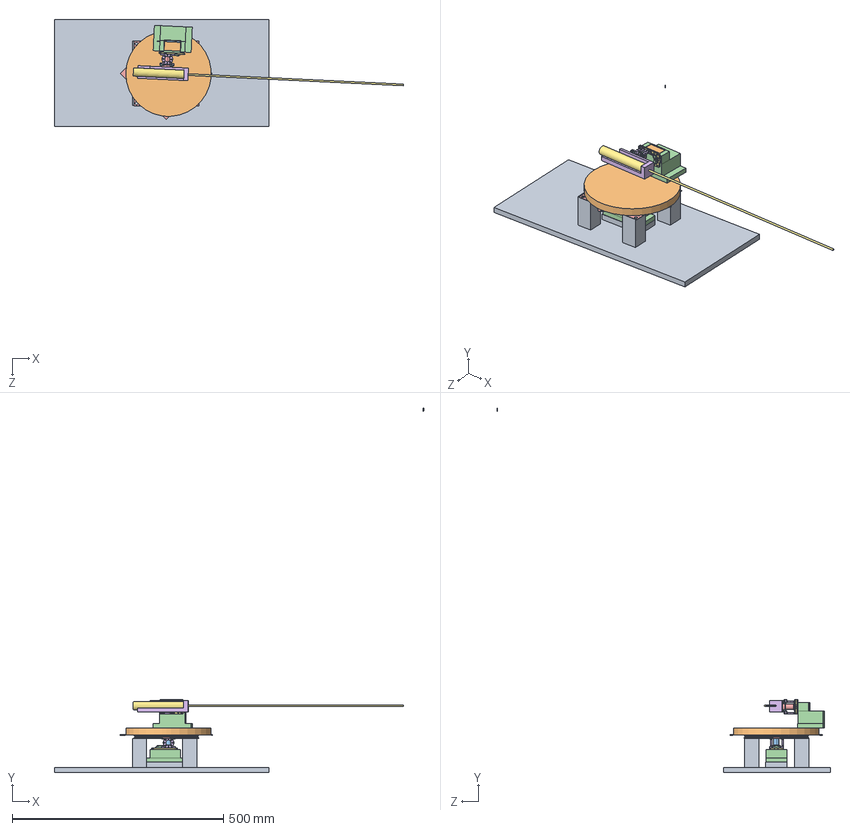
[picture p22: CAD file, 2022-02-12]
CAD Renderings/Base_v2.SLDASM
873.8 x 862.3 x 789.1 mm
Base_legs
User Library-Hitec HS-422 servo motor assy_Hitec HS-422 -001 x 2
User Library-Hitec HS-422 servo motor assy_Hitec HS-422 -002 x 2
User Library-Hitec HS-422 servo motor assy_Hitec HS-422 -003 x 2
User Library-Hitec HS-422 servo motor assy_c1 spline-001 x 2
User Library-Hitec HS-422 servo motor assy_servo_motor-005 x 2
User Library-Hitec HS-422 servo motor assy_copper_core_1 x 6
User Library-Hitec HS-422 servo motor assy_insulator_blk x 2
User Library-Hitec HS-422 servo motor assy_insulator_red x 2
User Library-Hitec HS-422 servo motor assy_insulator_ylw x 2
User Library-Hitec HS-422 servo motor assy_ISO 7049 - C-H ST 2.2 x 4.5 - C - H x 8
Servo Mount1 v4_imported
1544T100_LUBRICATED CORROSION-RESISTANT TURNTABLE
545420.step x 4
575112.step x 2
535118.STEP x 2
.5 x .75 non flanged bearing.STEP x 2
l1_pine
525122.step
Servo Mount2 v1_imported
DM v1_imported
Dowel

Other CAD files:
CAD Renderings/User Library-Hitec HS-422 servo motor assy_wire_red.sldasm
CAD Renderings/User Library-Hitec HS-422 servo motor assy_Hitec HS-422 -003.sldprt
CAD Renderings/User Library-Hitec HS-422 servo motor assy_ISO 7049 - C-H ST 2.2 x 4.5 - C - H.sldprt
CAD Renderings/User Library-Hitec HS-422 servo motor assy_c1 spline-001.sldprt
CAD Renderings/User Library-Hitec HS-422 servo motor assy_insulator_red.sldprt
CAD Renderings/User Library-Hitec HS-422 servo motor assy_servo hub.sldprt
CAD Renderings/User Library-Hitec HS-422 servo motor assy_servo_motor-005.sldprt
CAD Renderings/User Library-Hitec HS-422 servo motor assy_wire_ylw.sldasm
CAD Renderings/User Library-Hitec HS-422 servo motor assy_insulator_ylw.sldprt
CAD Renderings/User Library-Hitec HS-422 servo motor assy_Hitec HS-422 -001.sldprt
CAD Renderings/User Library-Hitec HS-422 servo motor assy_insulator_blk.sldprt
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

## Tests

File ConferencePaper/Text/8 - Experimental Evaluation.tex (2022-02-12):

Testing the fully assembled robot was conducted in two analogous but distinct phases, one for each configuration of AFER. Phase 1 tested the performance of AFER v1, and Phase 2 involved the same testing for AFER v2. The testing questions answered for both versions are listed below:
\begin{itemize}
\item Is the base adequately secured?
\item Does the up/down oscillation function under load?
\item Does the left/right oscillation function under load?
\item Does the combined oscillation function under load?
\item Do the chosen trajectories avoid self-collision?
\item Are the wires adequately concealed?
\item Have all obstacles been removed from the area?
\item Is the end effector securely attached?
\end{itemize}

Results for all tests were collected using visual observation, and servo outputs. Visual observation was the primary method of ascertaining proper behavior of the system, however the servo output data was also analyzed in real time to verify proper operation of the robot. Once the robot was determined to be operational and safe, the test subjects were introduced. 
The following procedure was used to ascertain the test subject’s interaction preferences between AFER v1 and AFER v2 robots and the type of end effector. Those steps were recorded and evaluated based on visual observation: 
\begin{itemize}
\item Introduce test subjects (cats) to base configuration
\item Assemble AFER v1
\item Introduce test subjects to v1 configuration
\item Allow test subjects to interact with operational AFER v1 with End Effector 1 attached
\item Allow test subjects to interact with operational AFER v1 with End Effector 2 attached
\item Observe and record test subject behavior
\item Repeat steps 2-6 with the AFER v2 configuration
\end{itemize}

Fig. 7 shows the engagement of kittens with AFER v1 and v2. Basic standards for ethical treatment of animals were obeyed when observing the cats/kittens engaged with the robots \cite{Brambell1965ReportOT}.

\begin{figure}[h!]

\caption{Kittens engaged with AFER v1 (left) and v2 (right).}
\end{figure}
